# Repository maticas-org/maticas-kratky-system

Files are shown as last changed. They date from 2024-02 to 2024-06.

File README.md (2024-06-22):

# Maticas Kratky System 🌱

In this project we built a modified kratky system which consists of the usual bucket but now incorporates additional oxigenation with an oxigen pump, the idea behind this was to test the results of adding micorrizae to the water and keep it alive inside the kratky system with this additional aeration, comparisson tests still remain to be done yet, however we've got good results with our basil crop test.

purple-full-spectrum-light-over-out-kratky-system
close-view-to-basil-plant

### Results of the basil growing test
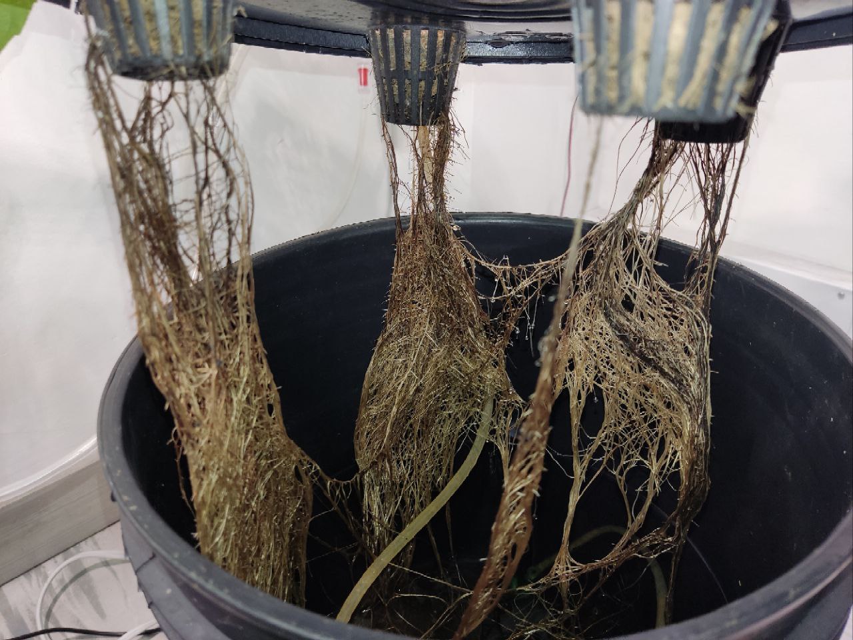
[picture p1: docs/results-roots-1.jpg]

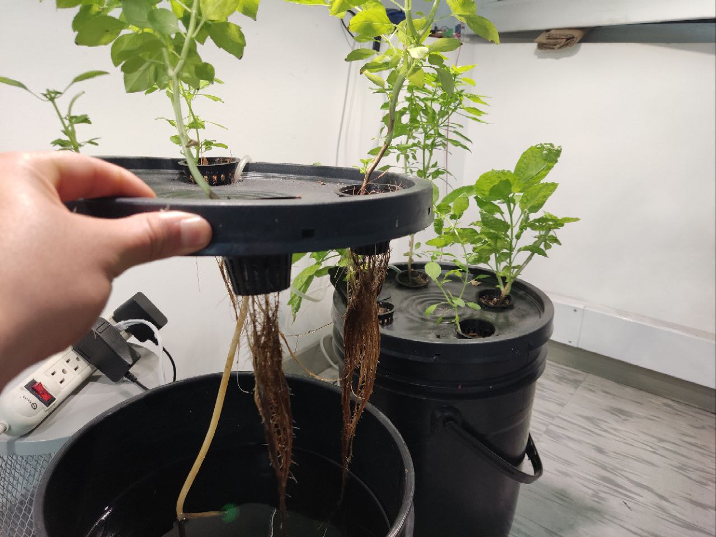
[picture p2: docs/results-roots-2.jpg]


All the plants are showing a good root development.

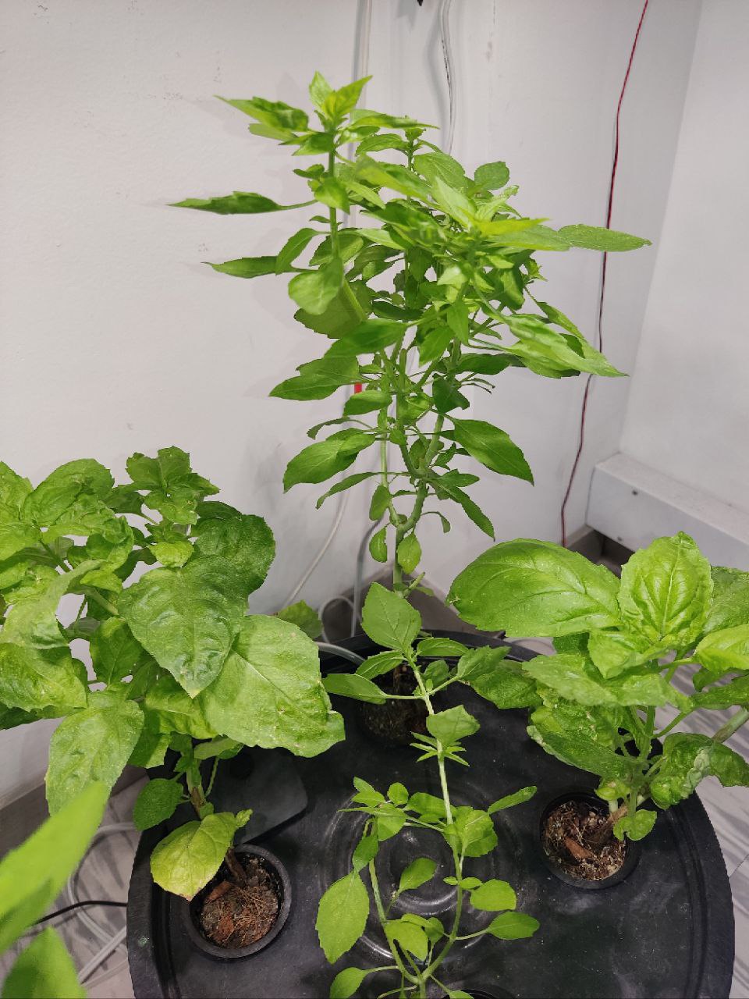
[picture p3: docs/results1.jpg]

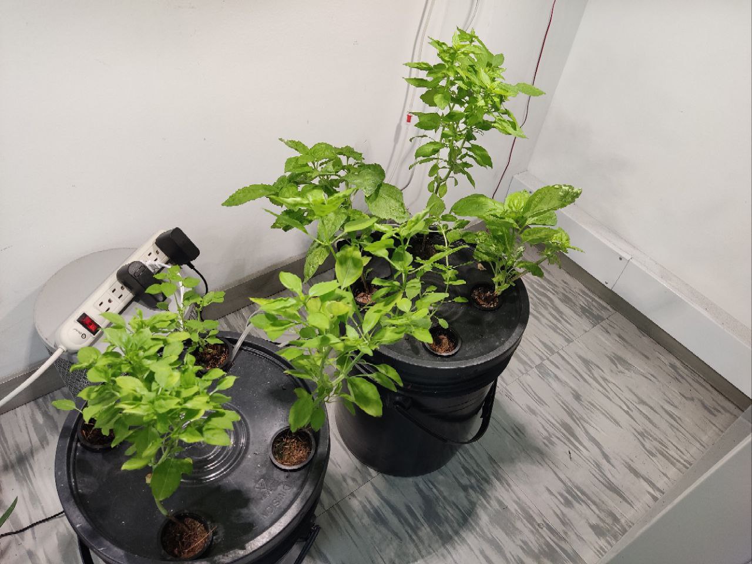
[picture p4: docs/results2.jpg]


And so far we've done 10 prunnings in about 2 months. It's true that we now have to develop a better concise and clear way to measure and compare results, but as far as building a system which allows plants to live with out concerning too much about taking care of the plants (5hr/month maximum) we've achived good results.

## Key features

- Capacity up to 8 plants with the current architecture for the growing system. 
- Measure ambient variables such as relative humidity and temperature, allows for extension and triggering of actions with this measurements.
- Control an AC actuator such as an oxigen pump _(We are expanding in order to control up to 3 AC actuators)._

- Local web server to monitor the conditions in the last 3 hours of operations of the device.
- Local web server available for modifying the periodicity and way the actuator works.
- Screen to display IP of the device in the local network and other desired data. 

<div style="display: flex; justify-content: center; align-items: center;">
  <div style="flex: 1; text-align: center; padding: 5px; height: auto; width: 45%;">
    root-growth-view-of-basil-plants
  </div>
  <div style="flex: 1; text-align: center; padding: 5px; height: auto; width: 45%;">
    web-server-of-app
  </div>
</div>

## Notes over the development 📝
root-growth-view-of-basil-plants

## Needed materials for replication ✅
### Structural materials

1. A pair of 20 liter containers [link to example product](https://articulo.mercadolibre.com.co/MCO-861436425-set-x-10-balde-cunete-20-litros-_JM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).

2. 8 cultivation baskets (or less depending on the space your plant needs) [link to reference product](https://www.amazon.com/Hydroponic-Plastic-Cultivation-Planting-Gardening/dp/B08R8LMF6L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).

3. Air pump [example pump](https://articulo.mercadolibre.com.co/MCO-828833010-motor-acuario-bomba-aire-oxigenador-pecera-sin-ruido-acuario-_JM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).

4. Aquarium air stone diffusers [example diffuser](https://www.amazon.com/Aquarium-Cylinder-Accessories-Aquariums-Hydroponics/dp/B0B5R4DPP4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).

5. 4 mt of silicone tube for air transportation a package like [this one](https://www.amazon.com/Airline-Tubing-Stones-Control-Connectors/dp/B0858ZSP7K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) can be really usefull because contains most of the elements we would need to use like:
- 1 check valve.
- 1 T shape conector for airline tubing. 

### Hardware materials

1. ESP32 module as there are many providers of ESP32 modules and they sometimes change the distribution of the pins I would recommend buying first the ESP32 and then checking if the PCB files we have need some previous small adaptation to fit the ESP32 module you got.
2. DHT11 or DHT22 _(you tecnically can use any sensor you want)_ feel free to modify the code if needed.
3. 10 kohm resistor for the DHT11 sensor as a pull up. 

pcb-view

## Contributing and TODOs 🔨💻

The following tasks are tasks yet to be done:

- Expand to control up to 3 AC actuators.
- Currently in terms of this architecture diagram we lack the implementation of the insight generator, and the Decision taker module which could be replaced by a PID or other mean of control so that the variables we need to control, we can control. 

<div style="background-color: white; display: inline-block;">
    Code architecture structure
</div>

- We are also learning on tiny ML to find new ways predictive tasks can be done in the embedded microcontroller and take better care of the plants.

- Any contribution you feel can be done we would be glad to help, any deploy you want to build we would be also happy to help. 

We are happy to help you, if you want to join or contribute to the project you can contact us in the following ways of communication that we leave below, also feel free to use the channels that github gives us.




## License Notice ⚖️

This project is licensed under two different licenses for different components:

### Hardware
All hardware designs in this repository are licensed under the **CERN Open Hardware Licence Version 2 - Strongly Reciprocal (CERN-OHL-S-2.0)**. 

You may use, study, modify, share, and distribute the hardware designs under the terms of the CERN-OHL-S-2.0. The full license text can be found in the `LICENSE.CERN-OHL-v2-Strongly-Reciprocal` file.

### Software
All software in this repository is licensed under the **GNU General Public License Version 3.0 (GPL-3.0)**.

You may use, modify, and distribute the software under the terms of the GPL-3.0. The full license text can be found in the `LICENSE.GPLv3` file.

---

**CERN Open Hardware Licence Version 2 - Strongly Reciprocal (CERN-OHL-S-2.0)**

Licensed under the CERN-OHL-S-2.0. You may obtain a copy of the License at [CERN-OHL-S-2.0 License](https://www.ohwr.org/project/cernohl/wikis/Documents/CERN-OHL-version-2).

**GNU General Public License Version 3.0 (GPL-3.0)**

Licensed under the GPL-3.0. You may obtain a copy of the License at [GPL-3.0 License](https://www.gnu.org/licenses/gpl-3.0.en.html).

---

Please refer to these licenses for details on your rights and responsibilities when using, modifying, and distributing components of this project.

## Acknowledgments 🤝🫂

Thanks a lot to Sergio Colmenares _(our expert in electronic engineering)_ for the testing, development and support with the electronics of this project along with the 3D box design for the protection of the electronics, without you this truly could not have been possible. The ideas and dedication you brought are amazing and hope to continue with this parthership :D.

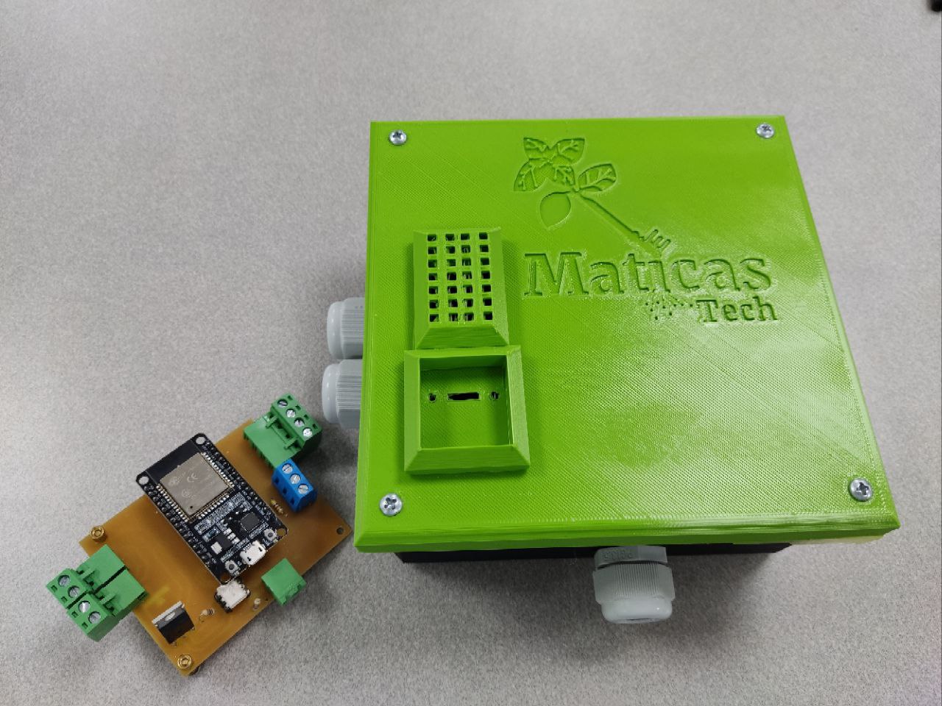
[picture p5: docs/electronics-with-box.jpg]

_this box by Sergio will be available soon in this repository_.

And last but not least at all thanks to Universidad del Rosario, particularly to the EICT team Nicolás Castiblanco, Katherine Escamilla, Julian for providing help on the ideation, PCB manufacturing and soldering, debugging, materials, good conversation and all the good times shared on the process you are great friends and support <3.      
Thanks to Rafael Mendez our Dean for facilitating all the space for constructing the project, the resources, trust and visibility that keeps us connecting with the right people and ideas, you are an example for us we want to follow <3.

## Donate 💸



If you have found this project helpful or if you think it is a good precedent you can support the development of Maticas by donating here:

<p align="center"><a href='https://www.buymeacoffee.com/DaveAlsina' target='_blank'>Buy Me a Coffee at ko-fi.com</p>

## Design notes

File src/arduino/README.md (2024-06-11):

# Dependencies

- [ArduinoJson](https://arduinojson.org/?utm_source=meta&utm_medium=library.properties) Version 7.0.4
- [NTPClient](https://github.com/arduino-libraries/NTPClient) Version 3.2.1

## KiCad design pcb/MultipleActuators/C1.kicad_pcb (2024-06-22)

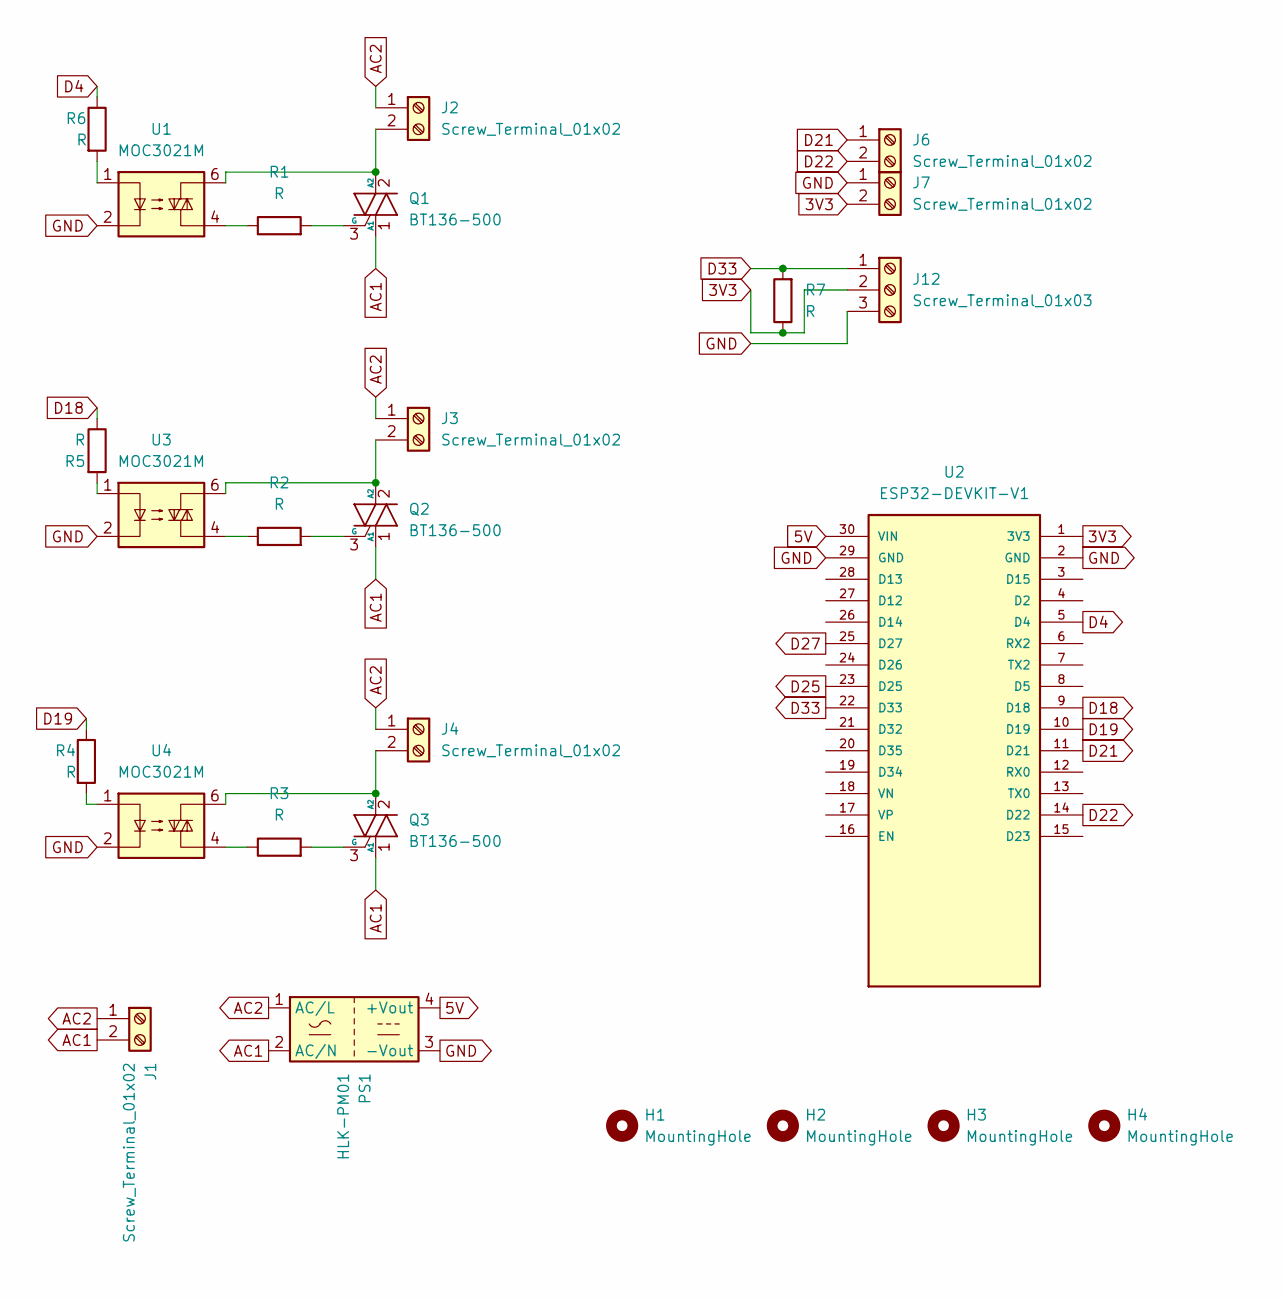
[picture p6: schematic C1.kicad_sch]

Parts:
H1, H2, H3, H4: MountingHole; MountingHole_3mm_Pad
J1, J2, J3, J4, J6, J7: Screw_Terminal_01x02; TerminalBlock_Altech_AK300-2_P5.00mm
J12: Screw_Terminal_01x03; TerminalBlock_Altech_AK300-3_P5.00mm
PS1: HLK-PM01; Converter_ACDC_Hi-Link_HLK-PMxx
Q1, Q2, Q3: BT136-500; TO-220-3_Vertical
R1, R2, R3, R4, R5, R6, R7: R; R_Axial_DIN0207_L6.3mm_D2.5mm_P2.54mm_Vertical
U1, U3, U4: MOC3021M; DIP-6_W7.62mm
U2: ESP32-DEVKIT-V1; MODULE_ESP32_DEVKIT_V1

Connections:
3V3: J7.2, J12.2, R7.1, U2.1 (3V3); also elsewhere on the board
5V: PS1.4 (+Vout), U2.30 (VIN)
AC1: J1.2, PS1.2 (AC/N), Q1.1 (A1), Q2.1 (A1), Q3.1 (A1)
AC2: J1.1, J2.1, J3.1, J4.1, PS1.1 (AC/L)
D4: R6.1, U2.5 (D4)
D18: R5.1, U2.9 (D18)
D19: R4.1, U2.10 (D19)
D21: J6.1, U2.11 (D21)
D22: J6.2, U2.14 (D22)
D25: U2.23 (D25)
D27: U2.25 (D27)
D33: J12.1, R7.2, U2.22 (D33); also elsewhere on the board
GND: J7.1, J12.3, PS1.3 (-Vout), U1.2, U2.2 (GND), U2.29 (GND), U3.2, U4.2
unnamed: J2.2, Q1.2 (A2), U1.6
unnamed: J3.2, Q2.2 (A2), U3.6
unnamed: J4.2, Q3.2 (A2), U4.6
unnamed: Q1.3 (G), R1.2
unnamed: Q2.3 (G), R2.2
unnamed: Q3.3 (G), R3.2
unnamed: R1.1, U1.4
unnamed: R2.1, U3.4
unnamed: R3.1, U4.4
unnamed: R4.2, U4.1
unnamed: R5.2, U3.1
unnamed: R6.2, U1.1

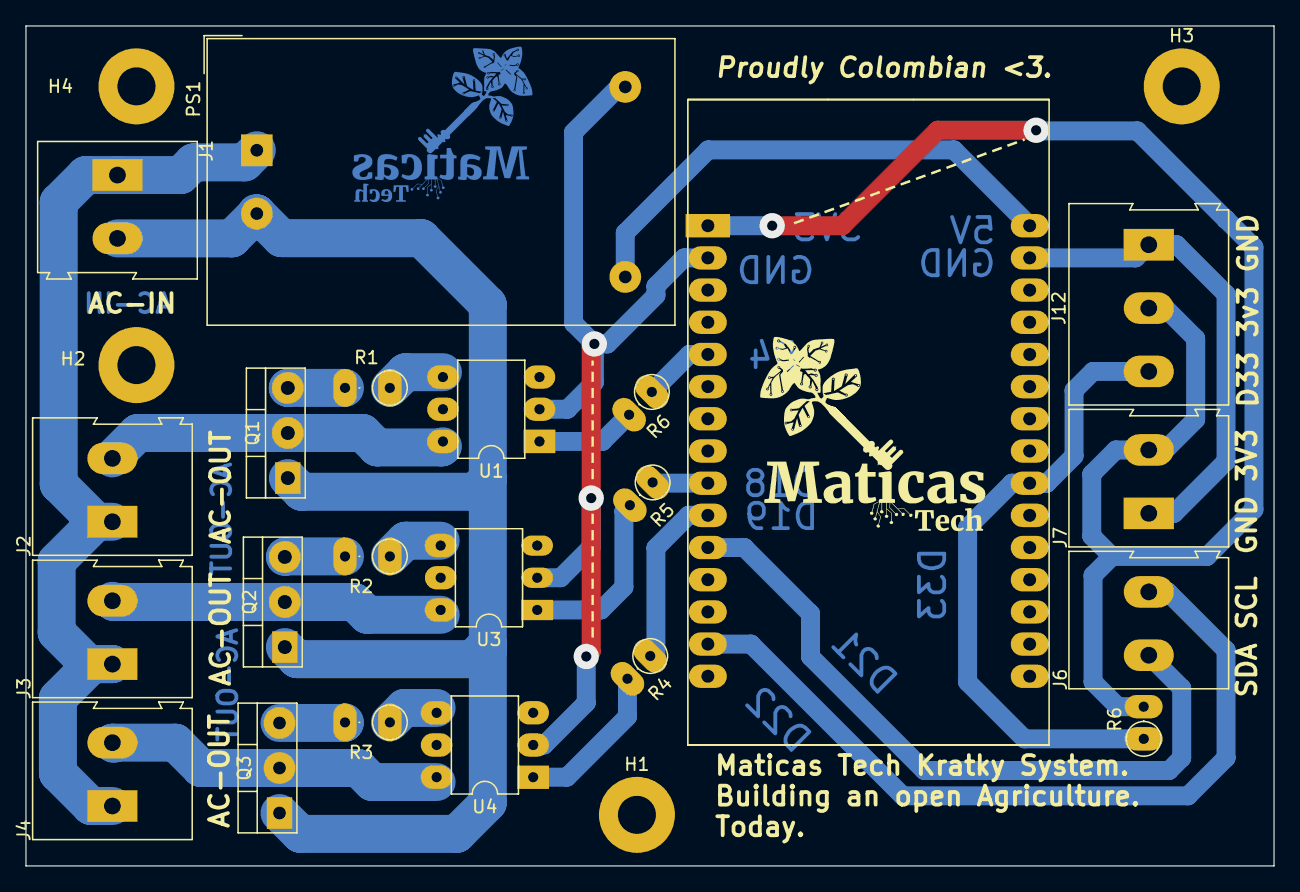
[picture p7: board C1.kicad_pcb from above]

Board: 2 copper layers, 98.5 x 66.3 mm, 26 parts (0 on the bottom side), 23 nets.

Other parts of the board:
R6#2: R; R_Axial_DIN0207_L6.3mm_D2.5mm_P2.54mm_Vertical

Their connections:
3V3: R6#2.2; also elsewhere on the board
D33: R6#2.1; also elsewhere on the board

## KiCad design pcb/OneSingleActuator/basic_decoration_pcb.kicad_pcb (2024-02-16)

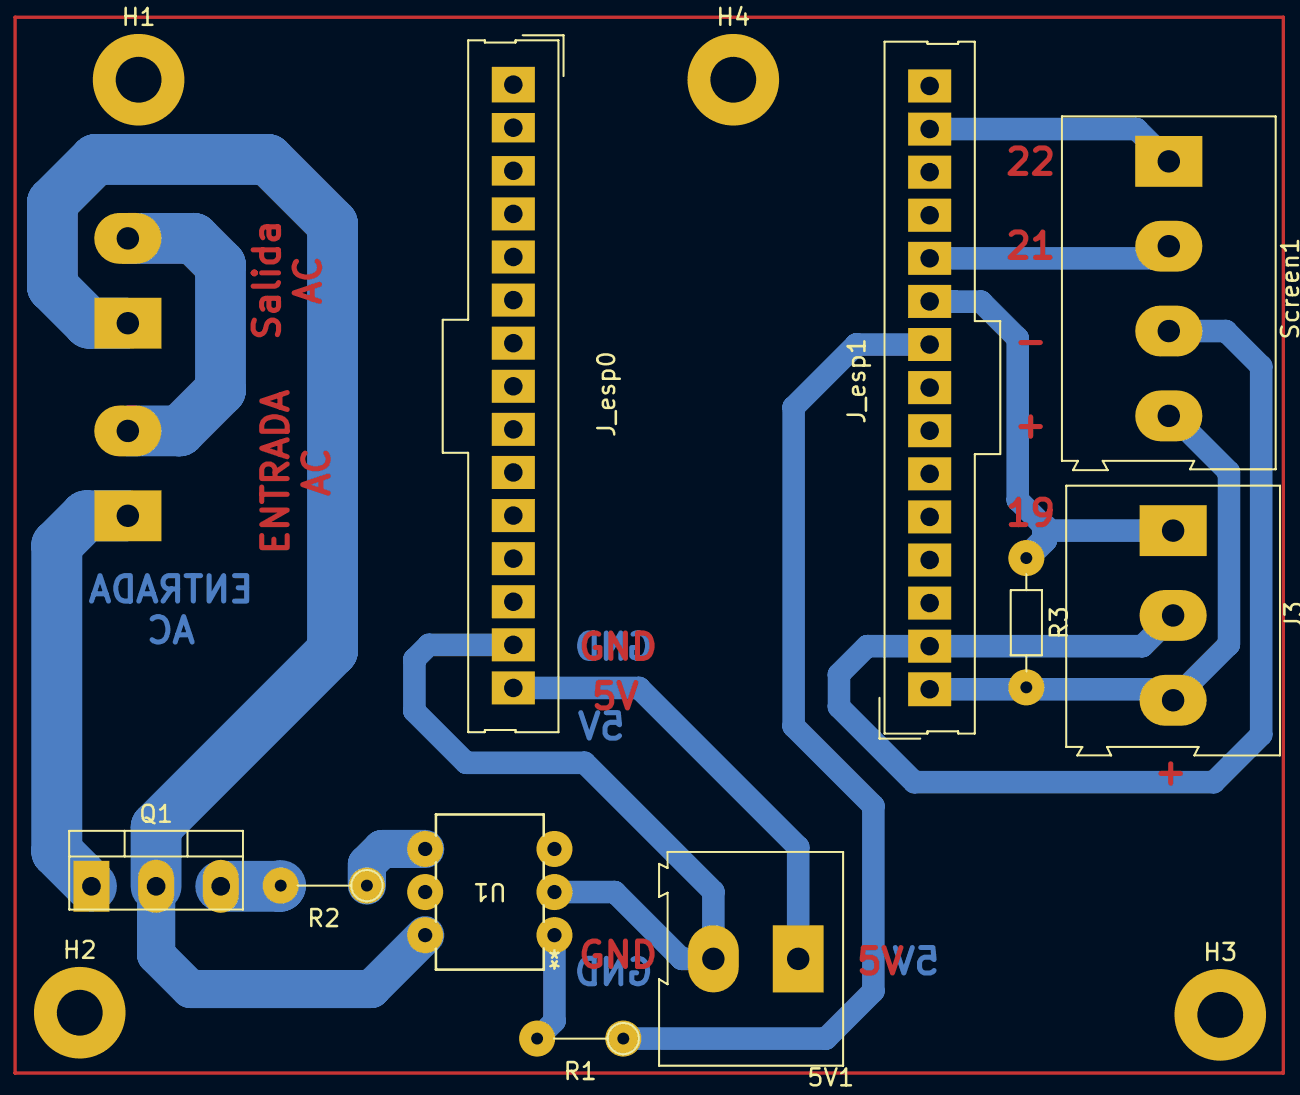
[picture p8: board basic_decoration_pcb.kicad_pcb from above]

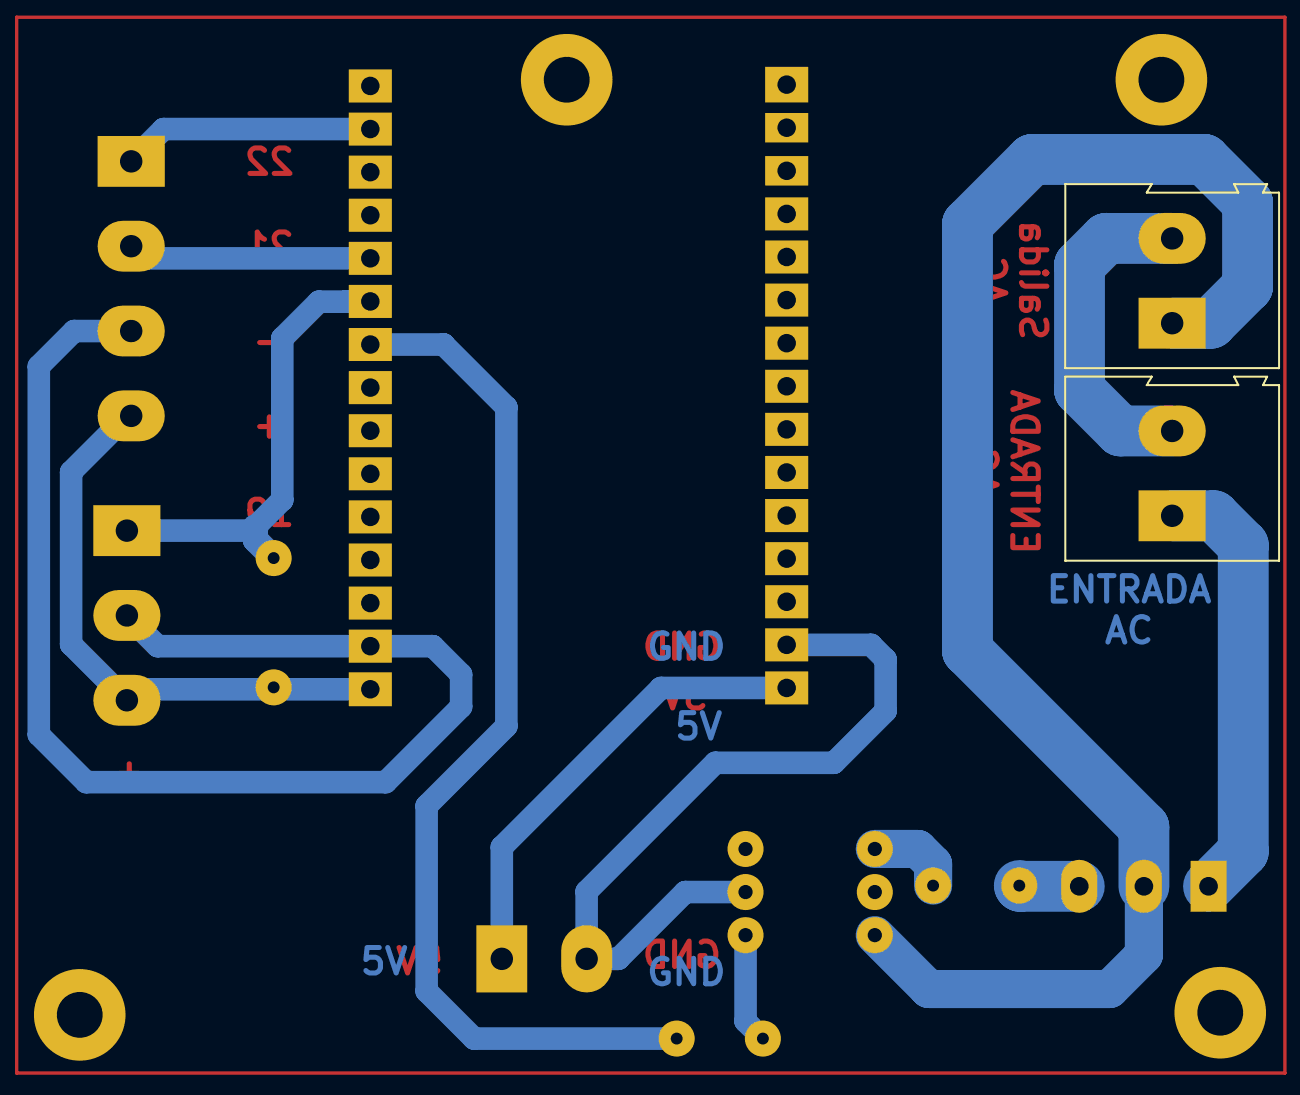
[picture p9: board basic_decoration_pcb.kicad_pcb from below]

Board: 2 copper layers, 16 parts (2 on the bottom side), 14 nets.

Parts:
5V1: Screw_Terminal_01x02; TerminalBlock_Altech_AK300-2_P5.00mm
H1, H2, H3, H4: MountingHole; MountingHole_2.7mm_M2.5_Pad
J3: Screw_Terminal_01x03; TerminalBlock_Altech_AK300-3_P5.00mm
J_AC_INPUT1: Screw_Terminal_01x02; TerminalBlock_Altech_AK300-2_P5.00mm
J_AC_LOAD1: Screw_Terminal_01x02; TerminalBlock_Altech_AK300-2_P5.00mm
J_esp0, J_esp1: Conn_01x15_Female; Connector_Molex_Molex_SL_171971-0015_1x15_P2.54mm_Vertical_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
Q1: BT136-500; TO-220-3_Vertical
R1, R2: 470; R_Axial_DIN0204_L3.6mm_D1.6mm_P5.08mm_Vertical
R3: 4.7k_0603; R_Axial_DIN0204_L3.6mm_D1.6mm_P7.62mm_Horizontal
Screen1: Screw_Terminal_01x04; TerminalBlock_Altech_AK300-4_P5.00mm
U1: MOC3041M; PDIP6_6P6X8P89_ONS

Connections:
3V3: J3.3, J_esp1.1, R3.2, Screen1.4
5v: 5V1.1, J_esp0.15
AC1_IN: J_AC_INPUT1.1, Q1.1 (A1)
AC2_IN: J_AC_INPUT1.2, J_AC_LOAD1.2
D18: J_esp1.9, R1.1
D19: J3.1, J_esp1.10, R3.1
D21: J_esp1.11, Screen1.2
D22: J_esp1.14, Screen1.1
GND2: J3.2, J_esp1.2, Screen1.3
GND5V: 5V1.2, J_esp0.14, U1.2
unnamed: J_AC_LOAD1.1, Q1.2 (A2), U1.6
unnamed: Q1.3 (G), R2.2
unnamed: R1.2, U1.1
unnamed: R2.1, U1.4

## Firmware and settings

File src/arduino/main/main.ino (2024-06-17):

#include <Arduino.h>
#include <ArduinoJson.h>
#include <Wire.h>
#include <WiFi.h>
#include <WiFiClient.h>
#include <WebServer.h>
#include <ESPmDNS.h>
#include <Preferences.h>
#include <Adafruit_SSD1306.h>

#include "InternetRTC.h"
#include "TimedOutput.h"
#include "HtmlPages.h"
#include "HandleConfigs.h"
#include "HandleWifi.h"

#define SCREEN_WIDTH  128 // OLED display width, in pixels
#define SCREEN_HEIGHT 64  // OLED display height, in pixels
#define OLED_RESET    -1  // Reset pin # (or -1 if sharing Arduino reset pin)
#define OLED_SYNC_INTERVAL 30000 // Sync screen every 30 seconds
Adafruit_SSD1306 display(SCREEN_WIDTH, SCREEN_HEIGHT, &Wire, OLED_RESET);

// Define sync interval
#define SYNC_INTERVAL 12*60*60*1000 // Sync time every 12 hours
#define SYNC_RETRY_INTERVAL 10000
#define SYNC_MAX_RETRIES 30
InternetRTC rtc; // Create an instance of the InternetRTC class

// Define output pin
#define OUTPUT_PIN_1 4
#define OUTPUT_PIN_2 18
#define OUTPUT_PIN_3 19

// Create instances of TimedOutput class for each output
TimedOutput output1(OUTPUT_PIN_1, "Lights");
TimedOutput output2(OUTPUT_PIN_2, "Fan");
TimedOutput output3(OUTPUT_PIN_3, "Water oxygenator");

ActuatorConfig defaultConf1 = {"Lights", OUTPUT_PIN_1, "on/off", DateTime(0,0,0,6,0,0), DateTime(0,0,0,18,0,0), 0, 0};
ActuatorConfig defaultConf2 = {"Fan", OUTPUT_PIN_2, "periodic",  DateTime(0,0,0,0,0,0), DateTime(0,0,0,0,0,0), 65, 65*4};
ActuatorConfig defaultConf3 = {"Water oxygenator", OUTPUT_PIN_3, "periodic", DateTime(0,0,0,0,0,0), DateTime(0,0,0,0,0,0), 65, 65*4};

// Define actuator configurations and configuration files
ActuatorConfig *actuatorConfigs[3] = {&defaultConf1, &defaultConf2, &defaultConf3};
Preferences preferences;

// Store this timed outputs in an array of pointers to the TimedOutput instances
TimedOutput *actuators[] = {&output1, &output2, &output3};

// Create an instance of the AsyncWebServer class
bool connected = false;
WebServer server(80);

// Tasks to run
TaskHandle_t Task1;
TaskHandle_t Task2;


// Method declarations
void mainControl(void *pvParameters);
void webServerTask(void *pvParameters);
void handleRoot();
void handleNotFound();
void handleWifiConfig();
void handleMakingChanges();
void handleUpdateActuatorConf();
void handleUpdateWifiConfig();


void setup() {
    // Initialize serial communication
    Serial.begin(115200);
    Serial.println("Starting Setup...");

    // Initialize display
    if(!display.begin(SSD1306_SWITCHCAPVCC, 0x3C)) { // Address 0x3C for 128x64
        Serial.println(F("SSD1306 allocation failed"));
    }

    // Connect to WiFi
    connected = connectToWiFi(preferences);

    // Initialize server
    if (MDNS.begin(MDNS_NAME)) {
        Serial.println("MDNS responder started");
    }
    delay(250);
    server.on("/", handleRoot);
    server.on("/makingChanges", HTTP_GET, handleMakingChanges);
    server.on("/wifiConfig", HTTP_GET, handleWifiConfig);
    server.on("/updateWifiConf", HTTP_POST, handleUpdateWifiConfig);
    server.on("/updateActuatorConf", HTTP_POST, handleUpdateActuatorConf);
    server.onNotFound(handleNotFound);
    server.begin();

    // Create tasks for the main control loop and web server
    xTaskCreatePinnedToCore(mainControl, "mainControl", 20000, NULL, 1, &Task1, 0);
    delay(500); 
    xTaskCreatePinnedToCore(webServerTask, "webServerTask", 20000, NULL, 1, &Task2, 1);
    delay(500); 

    // Initialize RTC
    rtc.syncInternetTime(SYNC_RETRY_INTERVAL, SYNC_MAX_RETRIES);

    // Load previous configurations and set actuators
    updateDefaultConfigs(preferences, actuatorConfigs, 3);
    for (int i = 0; i < 3; i++) {
        actuators[i]->setFromConfig(actuatorConfigs[i]);
    }
}

void loop() {
}


// Method to control actuators based on configuration
void mainControl(void *pvParameters){

    // Synchronize time every 10 minutes
    static unsigned long previousSyncTime = 0;
    // Sync screen every 30 seconds
    static unsigned long previousScreenTime = 0;

    while (true)
    {
        // Update output state based on current time
        for (int i = 0; i < 3; i++) {
            actuators[i]->updateOutputState(rtc.getCurrentDateTime());
        }

        if (millis() - previousSyncTime > SYNC_INTERVAL) {
            connected = checkWiFiConnection(preferences);
            rtc.syncInternetTime(SYNC_RETRY_INTERVAL, SYNC_MAX_RETRIES);
            previousSyncTime = millis();
        }else{
            rtc.syncLocalTime();
        }

        if (millis() - previousScreenTime > OLED_SYNC_INTERVAL) {
            screenDisplay();
            previousScreenTime = millis();
        }else if ( previousScreenTime == 0){
            screenDisplay();
            previousScreenTime = millis();
        }

        delay(500); 
        Serial.println();
    }
}

void webServerTask(void *pvParameters){
    while (true)
    {
        server.handleClient();
        delay(2);//allow the cpu to switch to other tasks
    }
}

void screenDisplay() {

    // Display the current date and time
    display.clearDisplay();
    display.setTextSize(2);
    display.setTextColor(SSD1306_WHITE);
    display.setCursor(0,0);
    display.println("Fecha-Hora");
    display.println(rtc.getCurrentDateTime().toString());
    display.display();
    delay(2000); // Display the time for 2 seconds

    // Display Maticas Tech URL
    display.clearDisplay();
    display.setTextSize(2);
    display.setTextColor(SSD1306_WHITE);
    display.setCursor(0,0);
    display.println("Visitanos en:");
    display.println("maticas-tech.com");
    display.display();
    delay(2000); // Display the URL for 2 seconds

    // Display the current device IP
    display.clearDisplay();
    display.setTextSize(2);
    display.setTextColor(SSD1306_WHITE);
    display.setCursor(0,0);
    display.println("Direccion IP: ");
    display.println(WiFi.localIP().toString());
    display.display();
    delay(2000); // Display the IP for 2 seconds

    // Display the logo
    display.clearDisplay();
    display.drawBitmap(0, 0, logo_bmp, SCREEN_WIDTH, SCREEN_HEIGHT, SSD1306_WHITE);
    display.display();
    delay(2000); // Display the logo for 2 seconds
}

// **************************************************************
// * Web server handlers
// **************************************************************

//---------------------------
// GET Requests handlers
//---------------------------
void handleRoot() {
  Serial.println("Handling /...");

  //check if the module is connected to the internet
  // if not, redirect to the wifi config page
  if (!connected) {
    server.send(200, "text/html", updateWifiConfig());
  }else{
    server.send(200, "text/html", updateConfigHTML(actuators, 3, rtc));
  }
}

void handleWifiConfig() {
  Serial.println("Handling /wifiConfig...");
  server.send(200, "text/html", updateWifiConfig());
}

void handleNotFound() {
  Serial.println("Handling unknown path...");
  String message = "File Not Found\n\n";
  message += "URI: ";
  message += server.uri();
  message += "\nMethod: ";
  message += (server.method() == HTTP_GET) ? "GET" : "POST";
  message += "\nArguments: ";
  message += server.args();
  message += "\n";

  for (uint8_t i = 0; i < server.args(); i++) {
    message += " " + server.argName(i) + ": " + server.arg(i) + "\n";
  }
  server.send(404, "text/plain", message);
}

void handleMakingChanges() {
  Serial.println("Handling /makingChanges...");
  server.send(200, "text/html", makingChangesHTML());
    
  // Allow some time for the client to receive the response
  delay(2000);

  // Reset the ESP32 to apply changes
  ESP.restart();
}

//---------------------------
// POST Requests handlers
//---------------------------
void handleUpdateActuatorConf() {
  Serial.println("Handling /updateActuatorConf...");
  // Check if the request has JSON data
  try{
    String i = server.arg("selected-actuator");
    String name = server.arg("name-" + i);
    String starttime = server.arg("starttime-" + i);
    String endtime = server.arg("endtime-" +i);
    String type = server.arg("type-" + i);
    String minuteson = server.arg("minuteson-" + i);
    String minutesoff = server.arg("minutesoff-" + i);

    // Update the configuration of the selected actuator
    ActuatorConfig actuatorConf = {name, actuators[i.toInt()]->pin, type, DateTime(starttime), DateTime(endtime), minuteson.toInt(), minutesoff.toInt()};
    saveActuatorConfig(preferences, &actuatorConf, i.toInt());
    actuators[i.toInt()]->setFromConfig(&actuatorConf);

    // Redirect to the root page
    server.sendHeader("Location", "/", true);
    server.send(302, "text/plain", "");


  } catch (const std::exception& e) {
    Serial.println("Error parsing JSON data");
    server.send(400, "text/plain", "Error parsing JSON data" + String(e.what()));
  }
}


void handleUpdateWifiConfig() {
  Serial.println("Handling /updateWifiConf...");
  // Check if the request has JSON data
  try{
    String ssid = server.arg("ssid");
    String password = server.arg("password");

    // Update the configuration of the selected actuator
    saveWifiConfig(preferences, ssid, password);

    // Redirect to making changes page
    server.sendHeader("Location", "/makingChanges", true);
    server.send(302, "text/plain", "");

  } catch (const std::exception& e) {
    Serial.println("Error parsing JSON data");
    server.send(400, "text/plain", "Error parsing JSON data" + String(e.what()));
  }

}

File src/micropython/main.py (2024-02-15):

import gc
gc.collect()
import scheduler
import modules.initialize_modules as mods

#turns off the actuators at the beginning
mods.act_mod.startup_off()

sch = scheduler.Scheduler(act_module = mods.act_mod,
                          sen_module = mods.sen_mod, 
                          screen_module = mods.screen_mod,
                          web_module=mods.web_mod,)
gc.collect()
sch.loop()

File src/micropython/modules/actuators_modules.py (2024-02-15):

#from machine import Pin
from utils.time_management_module import Time


#-----------------------------------------------------------------------------------------
#            ActuatorWrapper - extends and standarizes actuator pin capabilities 
#-----------------------------------------------------------------------------------------
class ActuatorWrapper:
    TIMED_TYPE = 'timed'
    ON_OFF_TYPE = 'on/off'

    def __init__(self, 
                 actuator_id: str,
                 actuator_name: str,
                 actuator_type: str,
                 actuator_pin: Pin,
                 start_time: Time,
                 end_time: Time,
                 minutes_on: int,
                 minutes_off: int,):
        
        self.id = actuator_id
        self.name = actuator_name
        self.type = actuator_type
        self.pin = actuator_pin
        self.start_time = start_time
        self.end_time = end_time
        self.minutes_on = minutes_on
        self.minutes_off = minutes_off

        # True if the actuator is on, False otherwise
        self.status = False 
        self.last_used = Time(-100, 0, 0)
    
    def off(self) -> None:
        self.pin.value(0)
        self.status = False
    
    def on(self) -> None:
        self.pin.value(1)
        self.status = True

    def timed_on_off(self,
                     now: Time) -> None:
        
        if self.type == ActuatorWrapper.TIMED_TYPE:
            self.handle_timed(now)
            print("actuator {} of type {} is {}".format(self.name, self.type, self.status))
        elif self.type == ActuatorWrapper.ON_OFF_TYPE:
            self.handle_on_off(now)
            print("actuator {} of type {} is {}".format(self.name, self.type, self.status))
        else:
            raise ValueError("actuator type not recognized")
    
    def handle_on_off(self,
                      now: Time) -> None:
        
        if (self.start_time > now) or (now > self.end_time):
            self.off()
        else:
            self.on()
    
    def handle_timed(self,
                     now: Time) -> None:
            
            if (self.start_time > now) or (now > self.end_time):
                self.off()
                return
    
            #if actuator is on, and it has been on for more than minutes_on, turn it off
            if self.status and ((now - self.last_used).to_total_minutes() > self.minutes_on):
                self.off()
                self.last_used = now
            
            #if actuator is off, and it has been off for more than minutes_off, turn it on
            elif (not self.status) and ((now - self.last_used).to_total_minutes() > self.minutes_off):
                self.on()
                self.last_used = now
    
    def __str__(self):
        return "ActuatorWrapper {}: {}, is {}".format(self.id, self.name, self.status)

    def __repr__(self): 
        return self.__str__()


#-----------------------------------------------------------------------------------------
#                      Actuators Module - controller for ActuatorWrappers
#-----------------------------------------------------------------------------------------
class ActuatorsModule():

    def __init__(self,
                 config_file: str):

        from ujson import load

        # reads the configuration file and stores it in a dictionary
        # for later instantiation of the connection
        with open(config_file) as f:
            self.config = load(f)

        self.actuators_config = self.config["actuators"]
        self.actuators = dict() # type: Dict[str, ActuatorWrapper]
        self.default_init()

    def startup_off(self) -> None:
        print("Starting up actuators...")
        for actuator in self.actuators.values():
            actuator.off()
            print("Actuator {} is OFF".format(actuator.name))
        print("Done! they are all OFF.\n")

    def default_init(self) -> None:
        from machine import Pin
        for actuatorId in self.actuators_config.keys():

            actuator = ActuatorWrapper(actuatorId,
                                       self.actuators_config[actuatorId]["name"],
                                       self.actuators_config[actuatorId]["type"],
                                       Pin(self.actuators_config[actuatorId]["pin"], Pin.OUT),
                                       Time(*self.actuators_config[actuatorId]["starttime"]), 
                                       Time(*self.actuators_config[actuatorId]["endtime"]),
                                       self.actuators_config[actuatorId]["minuteson"],
                                       self.actuators_config[actuatorId]["minutesoff"]) 

            self.actuators[actuatorId] = actuator


    def timed_control(self,
                      now: Time):

        for actuatorId in self.actuators_config.keys():
            self.actuators[actuatorId].timed_on_off(now)

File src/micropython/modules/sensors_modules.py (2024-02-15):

import gc
from json import load
from utils.time_management_module import *

import modules.initialize_database as db
#----------------------------------------------------------------------------------
#
#----------------------------------------------------------------------------------

class SensorWrapper:

    #use the instance of Database as a class attribute
    _database = db.db_mod

    def __init__(self, 
                 sensor_id: str,
                 sensor_name: str,
                 measure_every_some_time: Time):
        
        self.id = sensor_id
        self.name = sensor_name
        self.last_measured = Time(-100, 0, 0)
        self.measure_every_some_time = measure_every_some_time
        self.measurement_function = None

    @property
    def is_working(self) -> bool:
        """
            Tells wheter or not a measurement_function has been provided
            and therefore if the sensorwrapper works
        """
        return self.measurement_function != None

    def add_to_database(self, measurement: float):
        SensorWrapper._database.add_measurement(self.id, measurement)

    def set_measurement_function(self, fn: callable) -> None:
        self.measurement_function = fn

    def measure(self, now: Time) -> float:
        
        if (self.is_working):
            return self.measurement_function()
        elif (not self.is_working):
            raise ValueError("No measure function has been set")
            
    
    def timed_measurement(self, now: Time) -> float:
        """ 
            This function is used for checking if it's time to measure again.
        """

        if not self.is_working:
            print("Sensor {} is not working...".format(self.name))
            return None

        elif now - self.last_measured >= self.measure_every_some_time:
            self.last_measured = now
            measurement = self.measure(self.last_measured)
            print("{} value is: {}".format(self.name, measurement))

            self.add_to_database(measurement)
            return measurement

        else:
            print("We don't need the {} measurement yet, delta: {}".format(self.name, now - self.last_measured))
            return None

    def __str__(self) -> str:
        return "SensorWrapper: {} ({})".format(self.name, self.id)
    
    def __repr__(self) -> str:
        return self.__str__()

#----------------------------------------------------------------------------------
#
#----------------------------------------------------------------------------------

class SensorsModule():

    def __init__(self,
                 config_file: str):

        # reads the configuration file and stores it in a dictionary
        # for later instantiation of the connection
        with open(config_file) as f:
            self.config = load(f)

        self.sensors_config = self.config["sensors"]
        self.sensors = dict() #type Dict[str, SensorWrapper]
        self.default_init()

    def timed_measurement(self, now: Time):
        for sensor_id in self.sensors.keys():
            self.sensors[sensor_id].timed_measurement(now)

    def default_init(self) -> None:

        for sensor_id in self.sensors_config.keys():
            self.sensors[sensor_id] = SensorWrapper(sensor_id,
                                                    self.sensors_config[sensor_id]["name"], 
                                                    Time(*self.sensors_config[sensor_id]["measure_every_some_time"]),)

    def set_measurement_function(self,
                                 sensor_id: str,
                                 fn: callable) -> int:

        """
            Sets a measurement function 
        """

        if sensor_id not in self.sensors.keys():
            print("this sensor does not exist in the ACTUATORS field. Consider adding it in the file './config.json'.")
            return -1

        self.sensors[sensor_id].set_measurement_function(fn)
        print("Sensor {} added.".format(self.sensors[sensor_id].name))

        return 0

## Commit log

2024-02-16 Add kicad project
    [basic_decoration_pcb-B_Cu.gbr, basic_decoration_pcb-B_Mask.gbr, basic_decoration_pcb-B_Paste.gbr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]
2024-05-02 Update
    Refactor so that 2 code versions are available, the arduino flavour and the micropython flavour.
2024-05-02 Create
    Created the arduino version of the project from micropython, still lacks some features micropython has but incorportates an updated version which allows for multiple output use, for example now can u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
2024-05-02 Update
    Added the new PCB version and refactored "pcb" folder to allow for the two different versions of the pcb, the multiple output PCB is for a single layer PCB with some tricks.
    [C1-B_Cu.gbr, C1-B_Mask.gbr, C1-B_Paste.gbr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]
2024-05-11 bugfix, there was a mistake when storing settings from the http that was mapping all the outputs to pin 0, now it uses the previous pins instead of replacing them with constant cero
    [InternetRTC.cpp, main.ino]
2024-06-13 Update
    now handles the logic for connecting a new esp32 (with no wifi credentials associated)
2024-06-13 Update
    allows for mDNS use when working as AP, but when connecting to router the mDNS does not work any longer, tried also to add use of static IP when connecting to WIFI and works but it seems to conflict with the RTC time request, so avoided the use of it for WIFI connection.
    [main.ino]
2024-06-17 Update HtmlPages.h
    Titulos y logo de páginas actualizados
2024-06-17 Update main.ino
    Se añade lógica de manejo de LCD
2024-06-22 Update
    now this adds the HLK-PM01 so that this can have it's own AC-DC adapter built in, and has way more comfortable connection cable management inside a box. Next iterations will be replacing the connecto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
    [C1-B_Cu.gbr, C1-B_Mask.gbr, C1-B_Paste.gbr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]
